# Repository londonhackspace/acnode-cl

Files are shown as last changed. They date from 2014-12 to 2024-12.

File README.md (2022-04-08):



Table of Contents
=================

  * [Table of Contents](#table-of-contents)
  * [Features](#features)
  * [Parts list](#parts-list)
    * [For the transistor switch](#for-the-transistor-switch)
    * [For the rest of the node:](#for-the-rest-of-the-node)
    * [Making the transistor switch](#making-the-transistor-switch)
    * [Wiring in the arcade switch](#wiring-in-the-arcade-switch)
    * [How to get this running with a cooqrobot/elechouse pn532 breakout board:](#how-to-get-this-running-with-a-cooqrobotelechouse-pn532-breakout-board)
    * [Using the tool running pin](#using-the-tool-running-pin)
  * [Building and flashing the firmware](#building-and-flashing-the-firmware)
  * [Pin assignments:](#pin-assignments)
  * [using the CLI](#using-the-cli)
  * [Roles](#roles)
  * [Button status/colours:](#button-statuscolours)
  * [To use the button menu:](#to-use-the-button-menu)
    * [For maintainers the menu items are:](#for-maintainers-the-menu-items-are)
    * [So for a user to take a tool out of service:](#so-for-a-user-to-take-a-tool-out-of-service)
    * [For a maintainer to access the menu and do nothing:](#for-a-maintainer-to-access-the-menu-and-do-nothing)
    * [For a maintainer to add a card:](#for-a-maintainer-to-add-a-card)
  * [Glossary](#glossary)
    * [Offline and Online](#offline-and-online)
    * [In service and Out of service](#in-service-and-out-of-service)

# Features

* Command line interface for settings over the usb port

* Stores settings in eeprom

* Can log to a syslog server

* Uses DHCP to get it's ip address

* Optional pin to detect when a tool is running - good for detecting when consumables are being used

* Can record the total runtime of of the tool if the tool running pin is used.

* Button with RGB led for status.

* Single Button menu for adding cards and putting a tool off and online.

* Can cache 752 cards to the embedded eeprom.

# Parts list

## For the transistor switch

* 1 x NPN transistor, i used a 2N3904
* 1 x 1K resistor
* 1 x small bit (8 x 8 holes is fine) of Vero board
* 2 x C shaped crimp or solderable terminals for the relay
* 2 x wires with female header socket ends (the other end doesn't matter, and will be cut off), one black, and one red.
* 1 x black female to female header socket lead
* 1 x grey female to female header socket lead

## For the rest of the node:

* 2 x crimp or solderable spade terminals for the microswitch on the arcade button
* 2 x wires with female header socket ends (the other end doesn't matter, and will be cut off), one black & one white
* 1 x PN532 based card reader
* 1 x connected Launchpad TM4C1294XL
* 1 x red  female to female header socket lead
* 1 x blue female to female header socket lead
* 1 x green female to female header socket lead
* 1 x black female to female header socket lead

##  Making the transistor switch

* cut one end off the 2 wires with header socket ends, leaving as much wire
as possible and the female ends

* Strip the bare end crimp into the terminals - for the arcade button
terminals use a white and black wire, and for the relay use red and black
wires.

* Attach the red wire to the+ side of the VDC connections on the SSR and the
black one to the - side.

* Attach the red female and to +5v header pin on the launchpad

* On some strip board solder the transistor on one edge with the flat side
facing the rest of the board.

* Cut the track connected to the middle (base) pin of the transistor in the
middle of the board

* Solder the 1K resistor over the hole you've cut

* Solder a 3 pin header so the middle pin goes header -> 1k resistor ->
middle (base) of the transistor, and the left and right pins are connected
to the left and right pin of the transistor

Picture of stripboard + transistor + header:

https://pointless.net/photos/id/1419346624/

Picture of the bottom showing cut track:

https://pointless.net/photos/id/1419346632/

* with the header pins towards you looking edge on at the board (the flat
side of the transistor should be facing you), the pins are, from left to
right:

* 1 connect to GND on the connected launchpad with a black female to female lead.
* 2 connect to PG_1 on the connected launchpad
* 3 connect to - on the ssr VDC side with the black lead you made eairler

## Wiring in the arcade switch

* make two spade terminal leads, one white and one black

like this:

https://pointless.net/photos/id/1419334749/

* connect the black one to the bottom of the microswitch on the button and the other end to a convenient GND on the launchpad

* connect the white end to the terminal labelled "NO" on the microswitch, and the other end to PF_1 on the launchpad

* connect the white lead of the RGB led leads to +5V on the launchpad

* the RGB red, green and blue leads go to PM0, PM1 and PM2

## How to get this running with a cooqrobot/elechouse pn532 breakout board:

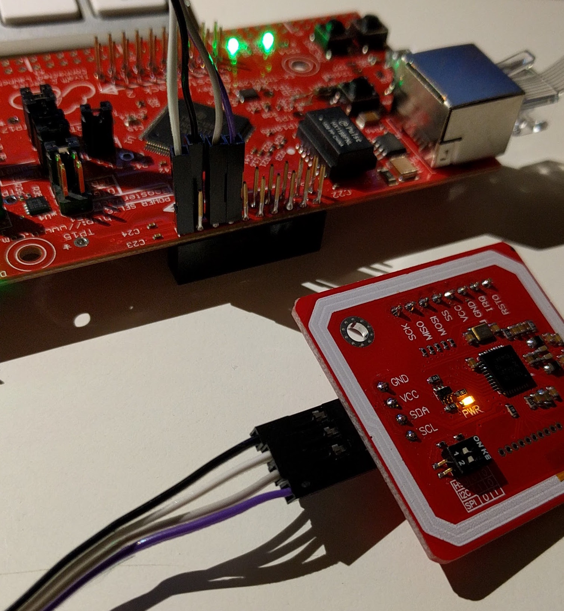
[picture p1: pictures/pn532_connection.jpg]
pn532 connected


1. Cooqrobot boards: Carefully unsolder the 0 ohm resistor jumper from the HIS0 connector, then resolder it (or just bridge the pads with solder) so that the '0' side is connected rather than the 1, this puts the reader in HSU mode.
  Elechouse boards: Set the DIP switches both to the right (This is as shipped from the factory) to put the reader into HSU mode.

2. Solder headers onto the 8 pin connector on the board where the TX/RX pins are, you need at least TX,RX,5V,GND. N.B. Cooqrobot boards: you can't use the SCL/SDA pins on the 4 pin connector because they have pullups on them...

2. Connect 5v and GND to somewhere convenient on the connected launchpad

4. This sketch uses Serial6 which uses PP0 and PP1, AKA pins 43 and 44 on the connected launchpad, connect those too, PP0 goes to TX on the board and PP1 to RX.

5. Check the labels on the card reader boards carefully, one cheap reader board has the pins for the FTDI cable pinouts *backwards* on the top (component) side of the board. Also some card readers label TX and RX the other way round... Do not use cheap Elechouse NFC Reader V3 clones - they often have the wrong component values in their antenna matching stage, and cannot energise cards well. Genuine Elechouse NFC Reader V4 (Direct from Elechouse, work well, the extra price is worth it for avoiding the hassle of deploying an under-performing reader).

See here for the Connected Launchpad pinouts:

http://energia.nu/pin-maps/guide_tm4c129launchpad/

## Using the tool running pin

You can send a signal to the acnode via pin PE_4 to say when your tool is actually running (as opposed to being switched on), useful for keeping track of wear and tear and consumables etc.

# Building and flashing the firmware

(non-PlatformIO version, tested on MacOS 10.12.6, 10.14.4 and Ubuntu 18.04)

* Install git for your platform if you haven't already
* Install cmake for your platform (http://cmake.org , debian/ubuntu package: cmake, MacOS homebrew: `brew install cmake`)
* Create a build directory `mkdir build`
* Run `./gettoolchain.sh`
* Update/initialise the git submodules `git submodule update --init`
* Use cmake to make a Makefile, and define your target board (EK-TM4C1294XL)
  `cd build && cmake .. -DCMAKE_TOOLCHAIN_FILE=../targets/tivac-launchpad/EK-TM4C1294XL.cmake`
  If building on MacOS, you may need to put the cmake binary on your path if you downloaded it manually or refer to it as
  /Applications/CMake.app/Contents/bin/cmake
* Use Gnu make to actually run the dependencies, compile and link: `make -j`
* When ready to upload the resultant elf binary to the Launchpad, `make -j flash`

# Pin assignments:

* PG_1 - active high, switches power to the tool, output
* PF_1 - the button, active low (uses internal pulllup), input
* PM_0 - RGB button Red channel, output
* PM_1 - RGB button Green channel, output
* PM_2 - RGB button Blue channel, output
* PP_0 - Serial RX from the card reader, input (should connect to TX on the card reader)
* PP_1 - Serial TX to the card reader, output (should connect to RX on the card reader)
* PE_4 - tool running pin, active low (uses internal pullup), input
* PD_0 - SD Card MISO (pin 7) aka D0
* PD_1 - SD Card MOSI (pin 2) aka CMD
* PD_3 - SD card clock (pin 5)
* PC_7 - SD card CS (pin 1) aka CD

# Pin assignments on ACNode shield rev 1 board (square PCB)

Other ACnode PCBs are available, the most common at the moment is the hardware/NEW-ACNode-Dootbot-Shield designed by dawidekziaja

* P1 connector (numbers rising towards on-board relay, P1_1 is furthest from it)
* P1_1 GND -> CAT5 ORANGE
* P1_2 +3.3V    NOT CONNECTED
* P1_3 PP0 RX ->  CAT5 WHITE/GREEN -> PN532 TXD
* P1_4 PP1 TX -> CAT5 GREEN -> PN532 RXD

* P3 connector (numbers rising towards reset button)
* P3_1 +3.3V
* P3_2 Red LED -> CAT5 BLUE
* P3_3 Green LED -> CAT5 WHITE/BROWN
* P3_4 Blue LED -> CAT5 BROWN

* P4 connector (numbers rising away from reset button)
* P4_1 +5V -> CAT5 WHITE/ORANGE
* P4_2 
* P4_3 GND

Button connector / Doorbell or ACnode menu button
* PF_1 SWITCH -> CAT5 WHTE/BLUE
* GND 

Door release button
* PM6 SWITCH -> Normally Open
* GND

* Note that Deek-Robot and Elechouse branded PN532 boards need +5V not +3.3v to function. 
Use the pinouts labelled on the back of the board.
Other boards (Genuine Elechouse NFC module v3) sort of work at +3.3V, but may not give sufficient juice to the NFC target to energise certain types of cards.

# Reader installation

For convenience of installation (acnode), and added security (doorbot), we recommend the reader module itself should be connected via an 8 wire cable, such as CAT5, and housed with a pushbutton NO switch and RGB LED in its own enclosure. This way, any intruder can't attack the reader and easily gain access. CAT5 (or above) wiring as above. Note the requirement for 220 ohm resistors on the Red/Green/Blue LED pins to prevent LED burnout. For operational convenience, it is advised to keep a spare reader that can be swapped out. Readers for doorbot enclosures can fit into standard single EN 60670-1 socket boxes with blanking plates, or outdoor junction boxes. For outdoor fitting, ensure that any holes for the button are suitably sealed against moisture ingress. Ditto for ACnode readers in a dusty or dirty environment. 

# Common reader enclosures

## ACnode role
Schneider Electric P/N SL00925 100x100x500 junction box smooth walls has been used for ACnode enclosures in the past. (Farnell DPN10/10 161706)
[ Internal free space 80x80x35mm to brim, there's 10mm outside of this area, compromised by the  mounting posts for the cover ]
[ Cover free space 80x80x16mm to brim, there's 10mm outside of this area, compromised by the mounting posts for the cover ]
Arcade Button with 5V Common Cathode RGB LED, from https://www.arcadeworlduk.com/, e.g. Ultralux RGB Illuminated Arcade Button, mounting hole required 28mm diameter hole in side of enclosure.
Mount PN532 reader and breakout board on the lid
(Optional - use RJ45 modular jack on the side of the enclosure and run a small patch lead to the breakout board, or find a suitable way of terminating the CAT5). Ideally, the readers are easily swappable between ACnodes, so mod jack on the side is a good plan.
Mount modular jack on opposide side of enclosure box to arcade button.

## Internal doorbot role

BS EN 60670-1 45mm deep single socket box with blanking plate
5V Common Cathode RGB LED
N/O SPST push button for doorbell. Choose one that doesn't accidentally get triggered while swiping.
Mount PN532 reader and breakout board on the blanking plate. Wire RJ45 CAT5 cable within walls.
## External doorbot role

British General WPJBS IP55 external junction box from B&Q
[ Internal free space 50x60x35mm, 8mm outide this space, compromised by the mounting posts for the cover ]
5V Common Cathode RGB LED
N/O SPST push button, *water resistant*. Choose one that doesn't accidentally get triggered while swiping.
Run CAT5 cable through a sealed grommit on the rear through the wall.

Pin Assignments
* +5V : RJ45_1 : WHITE/ORANGE : +5V
* GND : RJ45_2 : ORANGE : GND
* PP_0 : RJ45_3 : WHITE/GREEN : -> PN532 TXD
* PM_0 : RJ45_4 : BLUE : VIA R220 - RGB RED 
* PF_1 : RJ45_5 : WHITE/BLUE : the button, active low (uses internal pulllup), input
* PP_1 : RJ45_6 : GREEN : PN532 RXD
* PM_1 : RJ45_7 : WHITE/BROWN : VIA R220 - RGB Green
* PM_2 : RJ45_8 : BROWN : VIA R220 - RGB BLUE

# Power supply

For ACnodes, then a Power over Ethernet micro-USB power splitter works a treat. Feed the 5V USB power straight to the OTG micro USB connector near the ethernet jack, and jumper the Power Select to OTG. Make sure you connect to a network port that is supplied via a PoE network switch.
For doorbots, you will need +12V to power the door solenoid, and ideally, a battery backup. Feed the +12V into the London Hackspace doorbot board so that it goes via a regulator to supply +5V to the Launchpad via the BoosterPack connector. Jumper the launchpad's Power Select to OTG.

# using the CLI

Once the firmware has been uploaded to the connected launchpad connect with a serial terminal (if you use a real one rather than the Energia serial monitor you get command history and line editing).
It will work a lot better if it's connected to a working ethernet port with DHCP at this point.

Use `help` to see a brief description of commands. You want to set the nodeid and toolname as the minimum:

```
nodeid <id>
name <name of tool>
server <acserver hostname>
port <http port to use>
secret <shared secret, see acserver tool config>
syslog <syslog server to use>
mqtt_topic_base <mqtt_topic_base e.g. /tool/selfclearingdesk >
maintainercache - toggle maintainer cache mode (stores maintainers credentials in EEPROM so it should still work for maintainers after complete power loss)
```

and then `save` to save the settings.

It is good practice to make a note of the MAC address of the acnode, and reserve a DHCP reservation on the router for it, because then it can be monitored by icinga or other monitoring system.

# Button status/colours:

* Starting up: rainbow cycling
* In service, idle: blue
* In service, valid user, tool on: green
* In service, invalid user: red
* In service, maintainer: yellow
* Out of service, idle: flashing blue/red
* Out of service, valid user: red (and the tool will be off)
* Out of service, maintainer: yellow (and the tool will turn on)
* Doorbell pressed: Long Orange / Blue / Orange / Blue
* Door released: Green
* Door access denied: Red

# Roles

Each node can work in a variety of roles:

## Regular ACNode (0)

Provided that a card known to the system is presented, and it has access to this particular tool, the relay is active
as long as the card is on the reader.

## Doorbot (1)

Provided that a card known to the system is presented, the relay is activated for `KEEP_OPEN_MILISECONDS` (1.5 seconds).

## Doorbot with access control (2)

Provided that a card known to the system is presented, and it has access to this particular tool (door), the relay
is activated for `KEEP_OPEN_MILISECONDS` (1.5 seconds).

## Audit only (3)

Provided that a card known to the system is presented, the relay is active as long as the card is on the reader.
This is used primarily for logging what user was using a tool at what time.

# To use the button menu:

A short press starts the menu and switches between items, a long press selects a menu item.

For users the only menu item is to take the tool out of service - it's flashing red/green

The menu also times out after 60 seconds.

## For maintainers the menu items are:

* Add a user (flashing Amber)
* Take the tool out of service (if it's in service) - flashing red
* put a tool in service (if it's out of service), flashing green.

## So for a user to take a tool out of service:

Press the button once, quickly, the button will be flashing red/green.

Hold the button down for a second or so and release.

The button will go solid red and the tool will be out of service

## For a maintainer to access the menu and do nothing:

press the button once, the button will flash Amber/yellow - the ACNode is in add mode.

press the button again, the button will flash red/yellow - the menu is in take tool out of service mode.

press the button again, the button will stop flashing, you have exited the menu.

## For a maintainer to add a card:

Press the button, it will flash Amber/yellow

press the button for 1 second or so and let it go, the button will go yellow

remove the maintainer card. add the card to be added - the button will go orange (invalid card colour)

remove the card.

The new card should now be added.

# Glossary

## Offline and Online

The tool does not (or does) have a working network connection to the acserver. Things that can make an ACNode offline include:

* network cable unplugged
* Ethernet switch powered off or dead
* DHCP server down
* dns server down
* acserver VM down
* acserver VM running, but no acserver running
* acserver running, but crashing or having problems (e.g. database down, no cards in database)

## Nice to have services

The list of dependencies that are nice to have, but not strictly necessary

* mqtt server should be up, if announce_mode is set to mqtt (now default on new installs)

## In service and Out of service

Manually set by a maintainer or user - users can set a tool out of service, only a maintainer can put a tool in service, in/out of service state is kept in the acserver database and on the ACNode it's self
In doorbot or doorbot access control roles, in-service or out of service has no meaning, and has no way of setting this state, other than via the acserver itself.

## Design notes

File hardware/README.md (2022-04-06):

# How to make an ACnode or Doorbot

Over the years the design of the ACnodes and doorbots have been gradually improved.

As of 2021-10-28, all acnodes and doorbots in London Hackspace have been using the 'New-ACNode-Doorbot-Shield' designs. This is a single PCB designed to
fit **underneath** a TI Tiva C XL Connected Launchpad microcrontroller board EK-TM4C1294XL EVAL BRD, TIVA C CONNECTED LAUNCHPAD. The Launchpad boards are normally available from Farnell and RS.

There are plans for an all-new doorbot/acnode board together with a reader module, but they are not as yet ready for use. This is to address interference on long cable runs between the acnode/doorbot board and reader.

The board features an on-board 5V coil relay that is suitable for switching up to 10A of 230V. If you need to switch anything greater, then use it to
energise the coil of an appropriate contactor.

Build up the ACnode board as per kicad schematics. On rev 1.1b, component values are silkscreened for easy assembly. You will require long header pins so that the Launchpad board sits above the relay. Hint when soldering the long header pins into this board - use a Launchpad upside-down as a jig to hold the pins, place the pins, place the ACnode board upside-down, then solder them. Once soldered, a blob of hot glue is advised to keep the long header pins spaced and prevent bending them when handling in future.
When building the board for the ACnode role, you may omit the LM7805 voltage regulator if you're only going to be providing it with +5V power.

Always ensure that any metal enclosure is suitably earthed.

## Doorbot role

You will require

- A +12V power supply, approximately 3A at 12V should be enough to energise a maglock or solenoid lock. You can't use POE for this, it won't provide enough current for a maglock.
- Optional: A sealed lead acid battery, recommended for exterior doors. The doorbot software is designed to handle power outages with no networking available.
- A suitable helpfully labelled DOOR EXIT button, SPDT or DPDT, must be able to handle the current of whatever lock you choose. We will use two poles to both interrupt the current to the lock (NC contact) and to signal the doorbot to hold the door open for a time.
- Some CAT5 or higher wiring and connectors to run a cable to the reader module.
- Some suitable wire. We've found that old +12V DC power cables for CCTV cameras is suitable for the 12V lock circuit.
- A suitable enclosure
- A micro-USB to laptop cable, of suitable length, for configuration and flashing the software.
- A maglock with bracket, or solenoid deadbolt. 12V DC.

## ACnode role

You will require

- A +5V power supply, most decent USB power supplies work well, and you can get POE splitters that will provide this via Micro USB as well. Most of the London Hackspace network switches support POE. This is normally the recommended solution.
- Some CAT5 or higher wiring and connectors to run a cable to the reader module.
- Knowledge of the tool that you are providing access control to. Ideally, you'd be switching a low(er) voltage control circuit like an e-stop, rather than turning full power on and off to the tool. For high current switching, use an external suitably sized mains contactor.
- optional: a tool-running input, like on the laser cutter, the AC node can log the time the tool was running.
- suitable enclosure, or suitable space within the tool for the board. DIN rail mounting is recommended, 3D printed DIN-rail clips have been known to work with the board glued to the clips. Where we need a standalone enclosure, we have used TA 241911 ENCLOSURE BOX, GREY, IP65, 240X191X107MM, Farnell Part number 1422671
- A micro-USB to laptop cable, of suitable length, for configuration and flashing the software.

Set the power select jumper on the Launchpad board to 'OTG', and plug your USB power supply into the 'OTG' interface, we'll use that to provide power to the microcontroller.

## Reader enclosure

Typically used for ACnode roles.
Can use any suitable enclosure, but ideally one deep enough for the arcade button, and a RJ45 modular connector. https://uk.farnell.com/schneider-electric/dpn10-10/box-abs-103x103x56mm/dp/161706 has worked well.
For a laser-cut card holder front-end, see the dxf files in this repository's hardware/ directory. These will need M2.5 nylon nuts to hold the stack of laser cut acrylic together through to the front cover of the reader.
We have typically used arcade microswitch buttons with LED. " Ultralux RGB Illuminated Arcade Button " from Arcade World UK. https://www.arcadeworlduk.com/products/ultralux-rgb-illuminated-arcade-button.html

For doorbot roles, we typically build the readers into standard socket boxes with blanking plates. Exterior card readers will need a suitably watertight enclosure with a watertight button.
Drilling a standard EN 60670-1 thermosetting plastic blanking plate to fit LED and buttons makes them prone to cracking. Start with a tiny pilot drill, ideally in a drill press, and work up sizes. Fortunately, they are cheap and very easy to come by (wilko,screwfix,B&Q).
RJ45 termination to a modular jack is typically within the enclosure rather than external as on most of the acnode role readers.
PN532 RFID reader module: Set to HSS mode. Elechouse V4. Order direct from Elechouse. Do not skimp on ordering from aliexpress or ebay, because there are huge numbers of clones with AWFUL antenna matching circuitry.

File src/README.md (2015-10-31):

Table of Contents
=================

  * [Table of Contents](#table-of-contents)
  * [Features](#features)
  * [Parts list](#parts-list)
    * [For the transistor switch](#for-the-transistor-switch)
    * [For the rest of the node:](#for-the-rest-of-the-node)
    * [Making the transistor switch](#making-the-transistor-switch)
    * [Wiring in the arcade switch](#wiring-in-the-arcade-switch)
    * [How to get this running with a cooqrobot/elechouse pn532 breakout board:](#how-to-get-this-running-with-a-cooqrobotelechouse-pn532-breakout-board)
    * [Using the tool running pin](#using-the-tool-running-pin)
  * [You will need these libraries:](#you-will-need-these-libraries)
    * [Syslog from here:](#syslog-from-here)
    * [the PN532 libraries from here:](#the-pn532-libraries-from-here)
    * [DateTimeLibrary](#datetimelibrary)
    * [SD Card Library](#sd-card-library)
  * [Pin assignments:](#pin-assignments)
  * [using the CLI](#using-the-cli)
  * [Button status/colours:](#button-statuscolours)
  * [To use the button menu:](#to-use-the-button-menu)
    * [For maintainers the menu items are:](#for-maintainers-the-menu-items-are)
    * [So for a user to take a tool out of service:](#so-for-a-user-to-take-a-tool-out-of-service)
    * [For a maintainer to access the menu and do nothing:](#for-a-maintainer-to-access-the-menu-and-do-nothing)
    * [For a maintainer to add a card:](#for-a-maintainer-to-add-a-card)
  * [Glossary](#glossary)
    * [Offline and Online](#offline-and-online)
    * [In service and Out of service](#in-service-and-out-of-service)

# Features

* Command line interface for settings over the usb port

* Stores settings in eeprom

* Can log to a syslog server

* Uses DHCP to get it's ip address

* Optional pin to detect when a tool is running - good for detecting when consumables are being used

* Can record the total runtime of of the tool if the tool running pin is used.

* Button with RGB led for status.

* Single Button menu for adding cards and putting a tool off and online.

* Can cache 752 cards to the embedded eeprom.

# Parts list

## For the transistor switch

* 1 x NPN transistor, i used a 2N3904
* 1 x 1K resistor
* 1 x small bit (8 x 8 holes is fine) of Vero board
* 2 x C shaped crimp or solderable terminals for the relay
* 2 x wires with female header socket ends (the other end doesn't matter, and will be cut off), one black, and one red.
* 1 x black female to female header socket lead
* 1 x grey female to female header socket lead

## For the rest of the node:

* 2 x crimp or solderable spade terminals for the microswitch on the arcade button
* 2 x wires with female header socket ends (the other end doesn't matter, and will be cut off), one black & one white
* 1 x PN532 based card reader
* 1 x connected Launchpad
* 1 x red  female to female header socket lead
* 1 x blue female to female header socket lead
* 1 x green female to female header socket lead
* 1 x black female to female header socket lead

##  Making the transistor switch

* cut one end off the 2 wires with header socket ends, leaving as much wire
as possible and the female ends

* Strip the bare end crimp into the terminals - for the arcade button
terminals use a white and black wire, and for the relay use red and black
wires.

* Attach the red wire to the+ side of the VDC connections on the SSR and the
black one to the - side.

* Attach the red female and to +5v header pin on the launchpad

* On some strip board solder the transistor on one edge with the flat side
facing the rest of the board.

* Cut the track connected to the middle (base) pin of the transistor in the
middle of the board

* Solder the 1K resistor over the hole you've cut

* Solder a 3 pin header so the middle pin goes header -> 1k resistor ->
middle (base) of the transistor, and the left and right pins are connected
to the left and right pin of the transistor

Picture of stripboard + transistor + header:

https://pointless.net/photos/id/1419346624/

Picture of the bottom showing cut track:

https://pointless.net/photos/id/1419346632/

* with the header pins towards you looking edge on at the board (the flat
side of the transistor should be facing you), the pins are, from left to
right:

* 1 connect to GND on the connected launchpad with a black female to female lead.
* 2 connect to PG_1 on the connected launchpad
* 3 connect to - on the ssr VDC side with the black lead you made eairler

## Wiring in the arcade switch

* make two spade terminal leads, one white and one black

like this:

https://pointless.net/photos/id/1419334749/

* connect the black one to the bottom of the microswitch on the button and the other end to a convenient GND on the launchpad

* connect the white end to the terminal labelled "NO" on the microswitch, and the other end to PF_1 on the launchpad

* connect the white lead of the RGB led leads to +5V on the launchpad

* the RGB red, green and blue leads go to PM0, PM1 and PM2

## How to get this running with a cooqrobot/elechouse pn532 breakout board:

1. carefully unsolder the 0 ohm resistor jumper from the HIS0 connector, then resolder it (or just bridge the pads with solder) so that the '0' side is connected rather than the 1, this puts the reader in HSU mode.

2. Solder headers onto the 8 pin connector on the board where the tx/rx pins are, you need at least tx,rx,3.3v,gnd. N.B. you can't use the SCL/SDA pins on the 4 pin connector because they have pullups on them...

2. Connect 3.3v and gnd to somewhere convenient on the connected launchpad

4. This sketch uses Serial6 which uses PP0 and PP1, AKA pins 43 and 44 on the connected launchpad, connect those too, PP0 goes to TX on the board and PP1 to RX.

5. Check the labels on the card reader boards carefully, one cheap reader board has the pins for the FTDI cable pinouts *backwards* on the top (component) side of the board. Also some card readers label TX and RX the other way round...

See here for the Connected Launchpad pinouts:

http://energia.nu/pin-maps/guide_tm4c129launchpad/

## Using the tool running pin

You can send a signal to the acnode via pin PE_4 to say when your tool is actually running (as opposed to being switched on), useful for keeping track of wear and tear and consumables etc.

# You will need these libraries:

## Syslog from here:

https://github.com/londonhackspace/Syslog

put it in the libraries folder under your energia sketches folder

## the PN532 libraries from here:

https://github.com/londonhackspace/PN532

You'll need to copy or symlink PN532 and PN532_HSU into your energia-sketches libraries directory as well.

## DateTimeLibrary

https://github.com/londonhackspace/DateTimeLibrary

Best to clone directly to your Energia libraries folder.

If you a are using Energia 16 you will need to patch the energia code with this change:

https://github.com/energia/Energia/pull/741/files

## SD Card Library

https://github.com/rei-vilo/SD_TM4C

(and rename it to 'SD'), [also see](http://jasiek.me/2015/08/28/using-an-sd-card-with-a-ti-tiva-c-tm4129.html) for some more details.

# Pin assignments:

* PG_1 - active high, switches power to the tool, output
* PF_1 - the button, active low (uses internal pulllup), input
* PM_0 - RGB button Red channel, output
* PM_1 - RGB button Green channel, output
* PM_2 - RGB button Blue channel, output
* PP_0 - Serial RX from the card reader, input (should connect to TX on the card reader)
* PP_1 - Serial TX to the card reader, output (should connect to RX on the card reader)
* PE_4 - tool running pin, active low (uses internal pullup), input
* PD_0 - SD Card MISO (pin 7) aka D0
* PD_1 - SD Card MOSI (pin 2) aka CMD
* PD_3 - SD card clock (pin 5)
* PC_7 - SD card CS (pin 1) aka CD

# using the CLI

Once the firmware has been uploaded to the connected launchpad connect with a serial terminal (if you use a real one rather than the Energia serial monitor you get command history and line editing).

Use `help` to see a brief description of commands. You want to set the nodeid and toolname as the minimum:

```
nodeid <id>
name <name>
server <acserver hostname>
port <http port to use>
syslog <syslog server to use>
```

and then `save` to save the settings.

# Button status/colours:

* Starting up: yellow
* In service, idle: blue
* In service, valid user, tool on: green
* In service, invalid user: orange
* In service, maintainer: yellow
* Out of service, idle: flashing blue/red
* Out of service, valid user: red (and the tool will be off)
* Out of service, maintainer: yellow (and the tool will turn on)

# To use the button menu:

A short press starts the menu and switches between items, a long press selects a menu item.

For users the only menu item is to take the tool out of service - it's flashing red/green

The menu also times out after 60 seconds.

## For maintainers the menu items are:

* Add a user (flashing Amber)
* Take the tool out of service (if it's in service) - flashing red
* put a tool in service (if it's out of service), flashing green.

## So for a user to take a tool out of service:

Press the button once, quickly, the button will be flashing red/green.

Hold the button down for a second or so and release.

The button will go solid red and the tool will be out of service

## For a maintainer to access the menu and do nothing:

press the button once, the button will flash Amber/yellow - the ACNode is in add mode.

press the button again, the button will flash red/yellow - the menu is in take tool out of service mode.

press the button again, the button will stop flashing, you have exited the menu.

## For a maintainer to add a card:

Press the button, it will flash Amber/yellow

press the button for 1 second or so and let it go, the button will go yellow

remove the maintainer card. add the card to be added - the button will go orange (invalid card colour)

remove the card.

The new card should now be added.

# Glossary

## Offline and Online

The tool does not (or does) have a working network connection to the acserver. Things that can make an ACNode offline include:

* network cable unplugged
* Ethernet switch powered off or dead
* DHCP server down
* dns server down
* acserver VM down
* acserver VM running, but no acserver running
* acserver running, but crashing or having problems (e.g. database down, no cards in database)

## In service and Out of service

Manually set by a maintainer or user - users can set a tool out of service, only a maintainer can put a tool in service, in/out of service state is kept in the acserver database and on the ACNode it's self

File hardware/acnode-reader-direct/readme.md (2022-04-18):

# AC node / doorbot breakout board
rev 1.1a

Designed in kicad 6

designed to connect an RJ45 socket to an Elechouse V4 NFC module
without spaghetti wiring.

Inspired by Liam's solder-pad version.

Initial revision of this is targeted at EN 60670-1 socket back-boxes / blanking plate builds as used by Doorbots.
There's no reason not to use them for acnodes as well, but a near-future revision (possibly before ordering the boards)
will include support for the existing boxes used for AC node builds with the massive arcade buttons, by means of different
mounting holes.

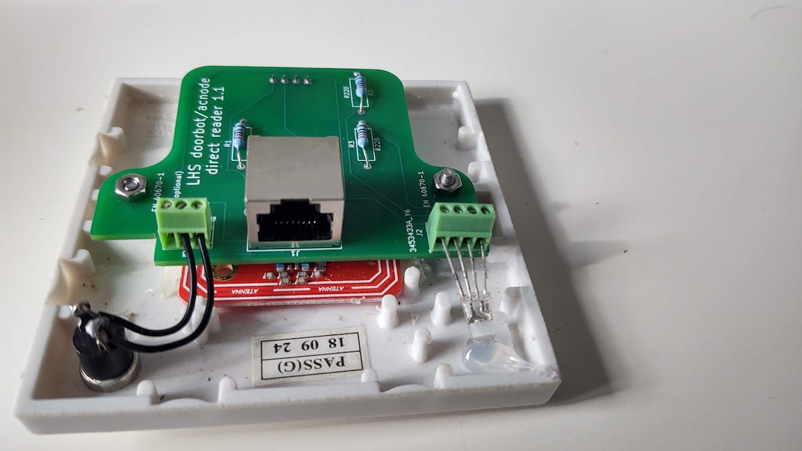
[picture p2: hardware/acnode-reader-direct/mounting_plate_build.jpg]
Blanking Plate build


# Errata

rev 1.1: J2 RGB LED silkscreen is labelled backwards. Should read B- G- +5 R-, with R- closest to the middle of the board, corrected in rev 1.1a

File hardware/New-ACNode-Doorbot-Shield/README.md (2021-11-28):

# acnode-doorbot
A board designed to be used for ACNode and Doorbot at London Hackspace
# Board View and 3D Render
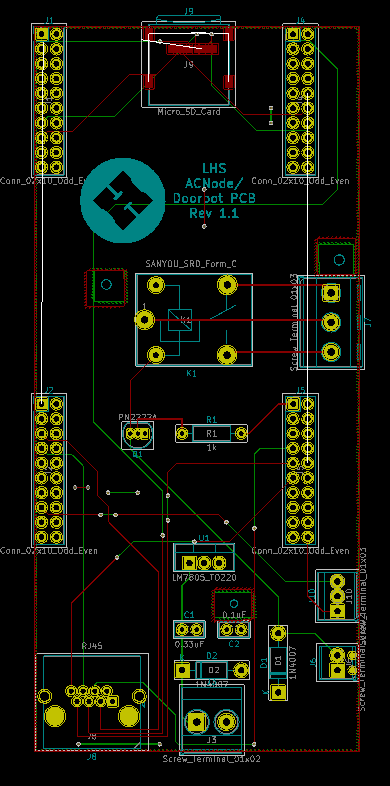
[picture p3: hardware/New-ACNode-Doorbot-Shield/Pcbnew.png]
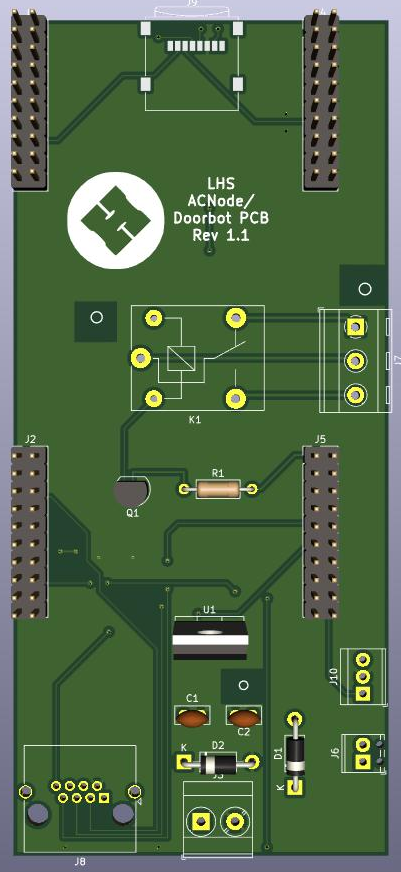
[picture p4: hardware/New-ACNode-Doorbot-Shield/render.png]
 

# Errata
rev 1.1 : RJ45 connector is round the wrong way
rev 1.1a : Relay outputs silkscreen is labelled incorrectly. NC is actually on the side closest to the SD card connector, not the voltage regulator side which is NO.

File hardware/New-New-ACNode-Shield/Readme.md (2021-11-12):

This is yet another board. IT IS NOT YET READY FOR USE!

It's basically a backport of the design I came up with for a Nucleo-based version. Key features include:
* An LED on the board for debugging
* A button on the board for debugging
* Support for RS-422 reader connection
* SPI Flash instead of SD Card
* Opto-isolated tool on input
* Trasistor-buffered door release with ferrite beads

Things to fix before the next version:

* Launchpad ethernet connector fouls the shield
* LED is... rather bright...
* A jumper on the ISL3176 ~RE line would allow a single board to support 5V and 12V readers
* Footprints for 3.81mm connectors are too tight - holes too small

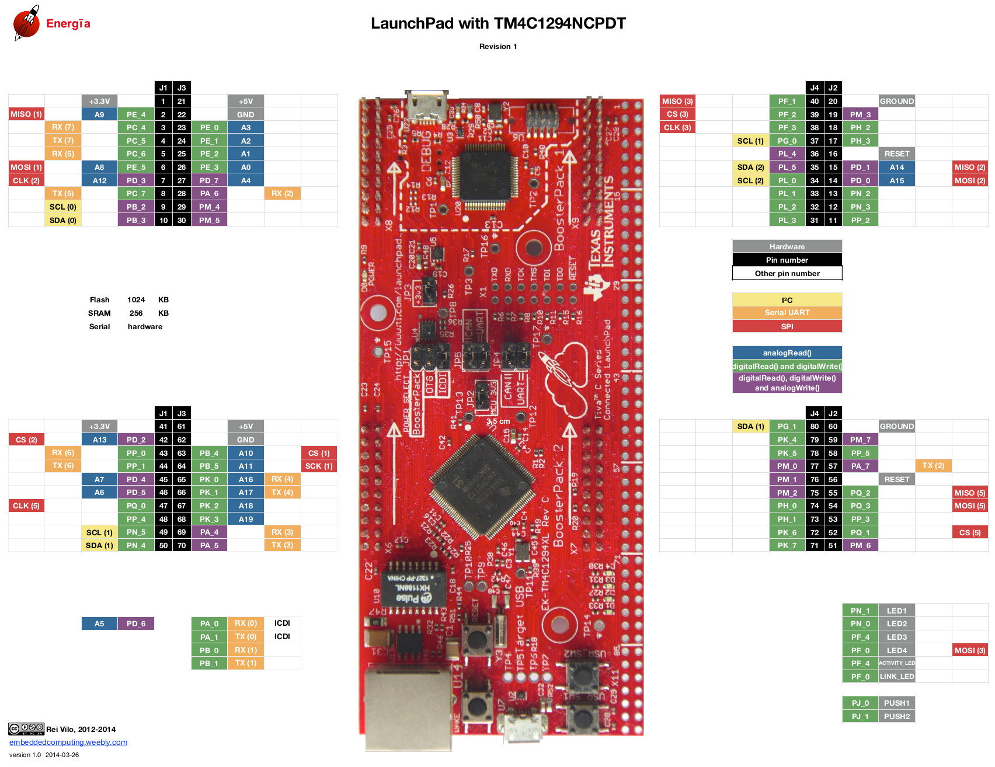
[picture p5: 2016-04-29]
pictures/EK-TM4C1294XL.jpg

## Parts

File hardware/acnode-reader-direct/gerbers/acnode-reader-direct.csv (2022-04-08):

Id | Designator | Package | Quantity | Designation | Supplier and ref
1 | J3 | TerminalBlock_TE_282834-3_1x03_P2.54mm_Horizontal | 1 | BUTTON N/O
2 | J1 | RJ45_Amphenol_RJHSE5380 | 1 | RJ45
3 | EN 60670-1,EN 60670-1 | MountingHole_3.7mm | 2 | MountingHole_3.7mm
4 | R1,R2,R3 | R_Axial_DIN0309_L9.0mm_D3.2mm_P12.70mm_Horizontal | 3 | R220
5 | J2 | TerminalBlock_TE_282834-4_1x04_P2.54mm_Horizontal | 1 | R- +5 G- B-
6 | LED HOLE | MountingHole_5.3mm_M5 | 1 | MountingHole_5.3mm_M5
7 | J4 | PinSocket_1x04_P2.54mm_Horizontal | 1 | Conn_01x04

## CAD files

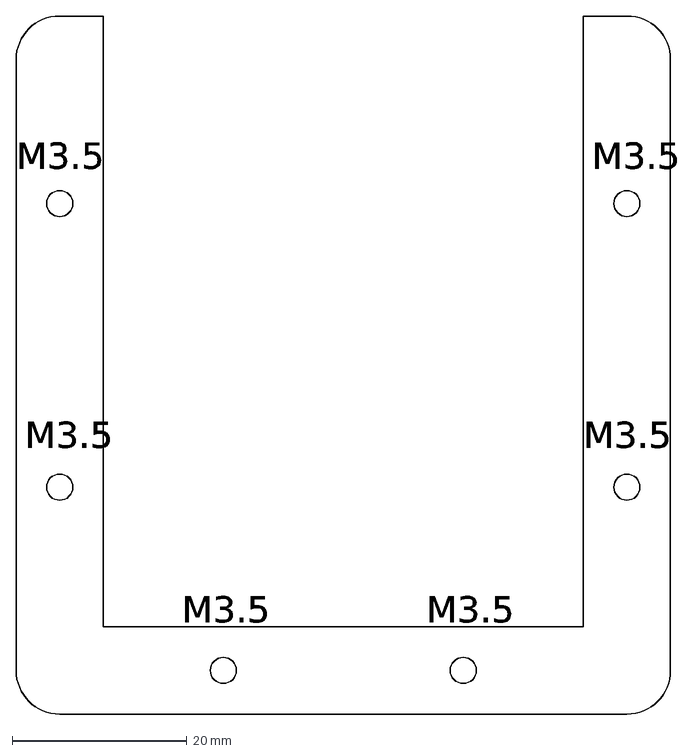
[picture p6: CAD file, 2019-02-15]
hardware/Card front middle.dxf
M3.5

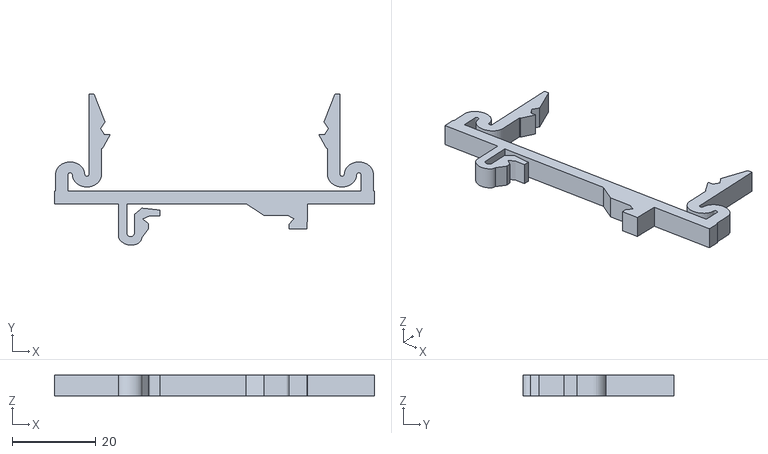
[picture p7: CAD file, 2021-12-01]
hardware/New-ACNode-Doorbot-Shield/dinrail_clip.stl
76.5 x 36.2 x 5.00

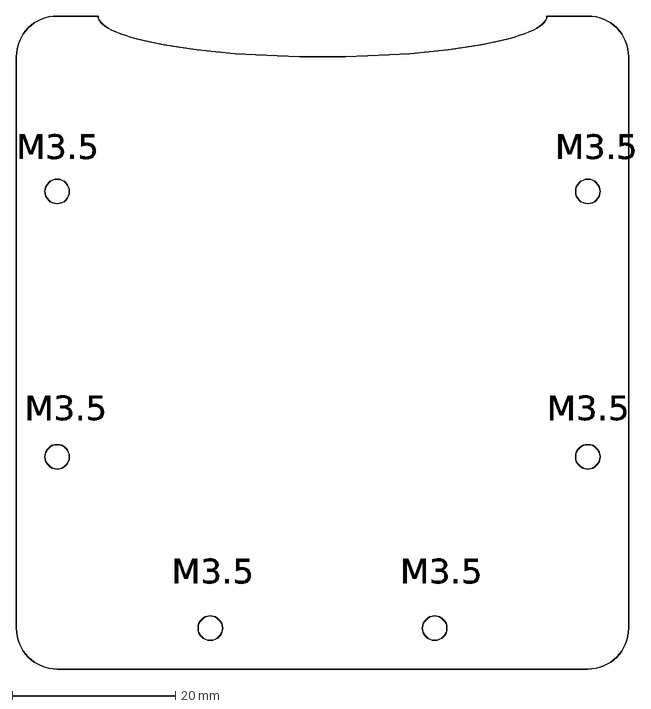
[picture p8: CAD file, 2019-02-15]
hardware/Card front.dxf
M3.5

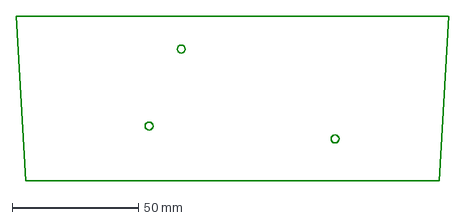
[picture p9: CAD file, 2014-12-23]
hardware/backing-frame.dxf
171.2 x 65.0 mm

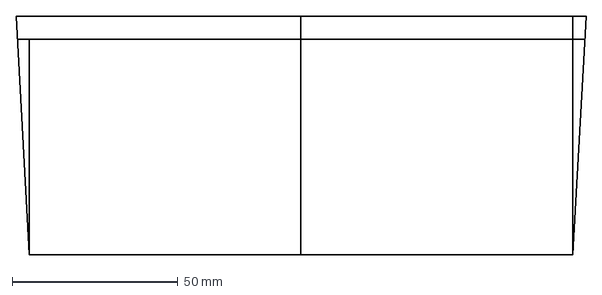
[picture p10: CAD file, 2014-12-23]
hardware/backing-v1.dxf
172.0 x 72.0 mm

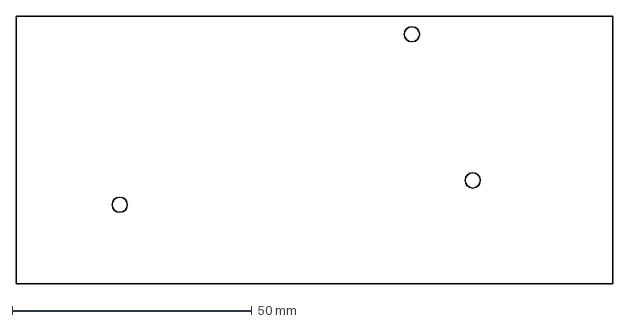
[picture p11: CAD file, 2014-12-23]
hardware/launchpad-footprint.dxf
124.5 x 55.9 mm

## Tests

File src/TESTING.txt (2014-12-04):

Check that:

A valid user switches the tool on
A vaild maintainer switches the tool on
A card that exists in the system but does not have perms does not switch the
tool on
A card that does not exist in the system does not switch the tool on

Check that card status changes correctly update the cache:

no perm -> perm
no perm -> maintainer
perm -> no perm
perm -> maintainer
maintainer -> no perm
maintainer -> perm

a maintainer can add a card
a maintainer can take an in service tool out of service (and is cached)
a maintainer can take an out of service tool in service (and is cached)
a normal user can take an in service tool out of service (and is cached)

check that cached users work when the acnode is disconnected
check that tool in service/out of service works when the acnode is disconnected

XXX what happend to tool status if we:

Are disconnected, a maintainer puts the tool out of service, the acnode is
reconnected and rebooted - it will query the server, the server will tell
the acnode that it should be in service and the acnode will put it back into service,
is that what we want?

Is the acnode or the acserver the authoritive source of the in/out of service status?

button colours:

tool starting up: yellow
tool in service, with net connection: blue
tool in service, no net connection: flashing orange/blue
tool out of service: red

Tool in service, and running: green
Tool in service, and running with a maintainer: yellow
Tool in service, card with no permissions: orange
tool in service, card not recognised: orange (would have to add more state
to recognise this case)

bugs:

clear does not work? (or maybe we need to re-read the settings?).
spams syslog if tool offline.
  - we need a "new user detected function"
the user stuff should be a class
new/delete, pointers and references, malloc and free is all a bit crazy.

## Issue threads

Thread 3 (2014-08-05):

work out what extra hardware we need and add them.

JasperWallace, 2014-08-05:
- RGB led?
- Reset button?
- Other button(s)? (e.g. "tool has failed button)
- methods of switching mains power on and off, we have an SSR, would be nice to have a range of options for different current draws
- last but not least, a decent enclosure

zymurgic, 2020-03-21:
Fairly stable set of acnodes has been deployed at Wembley. This ticket is old and can be closed.

Closed 2020-03-21.

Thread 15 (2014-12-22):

no pn532 reader with new connected launchpad

JasperWallace, 2014-12-22:
With a new connected launchpad the pn532 reader dosn't get initialised and the code hangs.

If you comment out all the stuff that calls the card reader, get to the cli, set a nodeid and save the settings the board can then talk to the card reader.

I have no idea why this happens :frowning: :confounded: :confused:

UKTamo, 2015-02-19:
Seems like new boards are Rev D that don't like working...

UKTamo, 2015-02-19:
Doesn't appear to be bringing the Tx line unto 3v3

Closed 2015-09-11.

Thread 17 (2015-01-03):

Add watchdog timer in case of crashes

russss, 2015-01-03:

JasperWallace, 2015-01-14:
http://forum.stellarisiti.com/topic/587-watchdog/
https://github.com/yuvadm/tiva-c/blob/master/boards/ek-lm4f232/watchdog/watchdog.c
https://github.com/energia/Energia/blob/master/hardware/lm4f/cores/lm4f/driverlib/watchdog.h
https://github.com/energia/Energia/blob/master/hardware/lm4f/cores/lm4f/driverlib/watchdog.c

Closed 2015-09-11.

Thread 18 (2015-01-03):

Laser cutter acnode crashes

russss, 2015-01-03:
We're seeing occasional crashes on the laser cutter acnode. This manifests itself either as the light staying blue when a card is presented, or the light staying yellow/green when the card is removed.

russss, 2015-01-03:
Adding watchdog (#17) may be enough to deal with this, at least initially.

JasperWallace, 2015-01-05:
if the watchdog times out it will powercycle the tool when the acnode restarts, better then nothing tho :disappointed: :crying_cat_face:

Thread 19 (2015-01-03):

Laser cutter acnode loses card

russss, 2015-01-03:
The laser cutter acnode is sometimes losing the card and switching the tool off.

This could be an issue with the card going out of range, as the reader is now stuck to the top of the box and there's no card slot.

However it should be noted that this has happened a few times when the card has definitely not moved at all. Additionally, it seems like moving the card around does not cause the acnode to re-acquire the card until the card has been completely removed and replaced. So there might be something else going on here.

zymurgic, 2019-03-19:
laser cutter acnode needs a bit of a rebuild to better match the other acnodes, with the reader in a slot.

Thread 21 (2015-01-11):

Check that we cope with running out of space to cache users, we already have 60 on the laser cutter!

JasperWallace, 2015-01-11:

JasperWallace, 2015-09-08:
We currently have 629 cards for the laser cutter.

An acnode using the eeprom for storage has space for 752 cards.

Closed 2015-09-08.

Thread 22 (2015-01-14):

minimum power on time

JasperWallace, 2015-01-14:
Some cards seem to glitch a little and only switch the acnode on for a fraction of a second. It's probably not good for the laser cutter when that happens!

So check how long we have been running on tool.off() and if < 1 second wait a few seconds before switching off.

Closed 2015-09-12.

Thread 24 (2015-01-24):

syslog logging is less verbose

JasperWallace, 2015-01-24:
It used to log:

local0.notice<133>: Jan 11 15:12:26 LaserCutter Tool On for 042B51BA5A1E80
local0.notice<133>: Jan 11 15:25:47 LaserCutter Tool off after running for 00:13:20 for 042B51BA5A1E80
local0.notice<133>: Jan 11 15:25:47 LaserCutter Total run time now: 00:13:20

but now just logs:

local0.notice<133>: Jan 12 14:34:22 LaserCutter Tool switched on for 04701E52E72280

The 'off'  and 'total run time' lines have got lost for some reason :disappointed:

UKTamo, 2015-01-24:
That's because tool time is done via the optothingy on the lasercutter

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

russss, 2015-01-24:
Yeah, we moved the time logging back to coolbot to try and debug the
crashing. We can probably put it back now that we know the new code wasn't
at fault.
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

JasperWallace, 2015-09-08:
ok, so not a bug

Closed 2015-09-08.

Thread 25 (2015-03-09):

Add a heartbeat

marksteward, 2015-03-09:
So we can see when the client dies, and catch failed "Access Finished" requests, so should probably include the "in-use" flag.

JasperWallace, 2015-03-10:
calling a uri on the acserver?

I can add a heartbeat eaisly with an Every().

marksteward, 2015-03-10:
Yeah! Like /ping or /heartbeat or summat. Happy to add the server-side

UKTamo, 2015-03-10:
Can we tie this into the ACNode checking acserver for status, and if the DB
says out of service, and the node says in service, the DB wins?

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

marksteward, 2015-03-10:
Yeah, maybe we should just call networkCheckToolStatus every minute. If the server doesn't see 3 requests in a row, it assumes the tool's no longer in use?

JasperWallace, 2015-05-10:
ead6d54bed62234c205fb647f28d224b559f47ab (and 972cccbbdfe9c13b47bd7feb1c9dbf3db78bf578) ended up calling networkCheckToolStatus every 2 seconds.

I can make that longer if needed, but part of that change was that we wanted a way to shut down a tool remotely, potentially in a hurry...

UKTamo, 2015-05-10:
Why an I getting these

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

JasperWallace, 2015-05-10:
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

You opened the bug originally, so github assumes you want to read the replies, I'm not sure if it possible to reassign a bug to someone else...

--

Jonty, 2015-05-10:
You can unsubscribe from the thread by hitting the "unwatch" button on the right.

UKTamo, 2015-05-10:
Ta

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

Closed 2015-05-10.

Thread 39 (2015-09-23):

watchdog will timeout if no network cable attached

JasperWallace, 2015-09-23:
I think dhcp had a 60 second timeout.

JasperWallace, 2015-09-27:
actually it doesn't, not sure what happened then...

Closed 2015-09-27.

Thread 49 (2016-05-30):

Replace the colour coded RGB button with something colour blind friendly

mentarus, 2016-05-30:
The single RGB button was a great idea for a simple interface but it makes it impossible to distinguish the state of the machine for some colour-blind maintainers. I don't think there's an "easy" solution for this, maybe adding a simple LCD screen should be considered?

russss, 2016-05-30:
A cheap LCD is going to be equally inaccessible to those with bad eyesight. Do we have someone who's red-blue colour-blind?

mentarus, 2016-05-30:
red-green actually

russss, 2016-05-30:
OK, I think we could sort it out with a software tweak. I'll give it a think.

JasperWallace, 2016-05-31:
I'm happy to run some tests with different colours to find ones that can be distinguished

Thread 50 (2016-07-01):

MicroSD slot on the PCB is the wrong size, needs adjusting.

jasiek, 2016-07-01:
Pads for the MicroSD holder are not correctly aligned with the actual part - needs redoing.

zymurgic, 2019-03-25:
We've got a new PCB design anyway, and the micro SD hinges fit this one fine.

Closed 2019-03-25.

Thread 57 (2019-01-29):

acnodes need to fail gracefully in event of network failure to acserver

zymurgic, 2019-01-29:
In the event of network failure between a booted acnode and acserver, it shouldn't mis-interpret the failure to connect to acserver as a tool-should-be-out-of-service error.
especiallly when the tool is currently in use.
it should also be able to gracefully fall back to using cached credentials, especially where it's using sdcard or eeprom card caches.

Today, this occurred when a network switch crashed and failed to forward packets), taking out both the 3d printers.

zymurgic, 2019-07-09:
acserver has been moved to the same VLAN as the acnodes themselves, which removes one point of failure. Still reliant on working network switches, but no longer reliant (at least from a packet-forwarding perspective) on a working router/firewall. Still requires DHCP leases to be able to renew or fail gracefully; A working DNS resolver is still very useful.

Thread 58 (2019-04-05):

Lasercutter node seems to be VERY chatty on syslog

mich181189, 2019-04-05:
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

I wonder if these log messages are related the weird run times we're seeing?

zymurgic, 2019-07-08:
If it pages down, or seeing frequent restart messages,  worth noting the acnode is currently powered via the attached Windows PC, which some people shut down. Maybe worth using PoE or similar instead?

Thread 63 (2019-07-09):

When DNS fails, mqtt (and other things) can cause reboots

mich181189, 2019-07-09:
When DNS is down, the resulting connection failures can cause the watchdog timer to be triggered. This is bad because it means the cache is lost

mich181189, 2019-07-13:
When dns fails once things are running, the node will work for a while before potentially getting stuck in a reboot loop.

What’s nasty is this can happen even if there is a cached card, because of the rebalidation.

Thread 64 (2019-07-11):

Unexplained hang of 1st floor dootbot

zymurgic, 2019-07-11:
Power was good to launchpad. 4.65V at VBUS should be good enough.
No response to card reader, or doorbell
No response to serial console.
No repsonse to ICMP.
Reset button fixed it.

mich181189, 2019-07-11:
4.65 sounds a little marginal to me. The microcontroller can, no doubt, handle it fine considering it's a 3.3v part, but I wonder how the board overall deals with it?

mich181189, 2019-07-12:
Launchpad is specified for 4.75-5.25v (source: http://www.ti.com/lit/ug/spmu365c/spmu365c.pdf section 1.6)

zymurgic, 2019-07-12:
will replace the regulator next time I'm in if nobody gets there sooner.

mich181189, 2020-03-20:
Power supply was out of spec - closing this one since it’s otherwise too vague to work on

Closed 2020-03-20.

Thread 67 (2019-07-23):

(hardware) Use of TIG welder near a doorbot reader cable run can fake a doorbell input

zymurgic, 2019-07-23:
Use of a TIG welder (other spark gap transmitters are available) in the vicinity of a doorbot reader cable can induce sufficient negative current in the input to trigger a doorbell notification.
Doorbell / button input is PF_1 on the Launchpad / White/Blue on the CAT5 / pin5, and is normally open, pulled to ground when pushed.

This may affect all microcontroller inputs, and may also be the cause of reported acnode crashes.

Investigate methods of input protection to attempt to prevent this.

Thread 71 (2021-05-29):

Maglock power sense

padski, 2021-05-29:
This is possibly included in a future HW update by Mich, adding here for the record.
Maglock power sense / tool on / door solenoid ..........
It would be great to know when our doors unlock themselves for whatever reason ;)

zymurgic, 2021-08-12:
The solenoid deadbolt locks have a 'door closed' output, which signals when it's properly closed. Those aren't currently wired in, but could go to a 'tool running' input, probably via some optocoupler. Then it's down to the acnode role as doorbot to detect and announce accordingly, which would be alarming or of interest in certain circumstances. However, where the exit button isn't also wired into the door release input but instead only interrupts the +12V power to the solenoid, the acnode wouldn't be aware of the reason for the door opening.

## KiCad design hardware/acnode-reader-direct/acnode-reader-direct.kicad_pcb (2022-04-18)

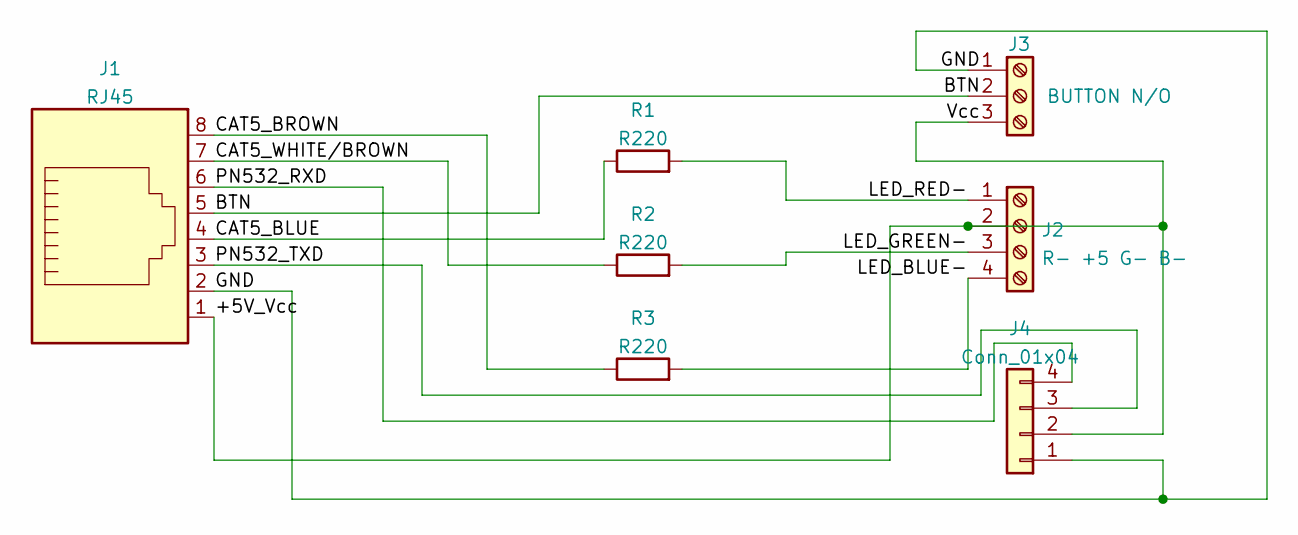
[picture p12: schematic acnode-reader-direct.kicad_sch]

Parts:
J1: RJ45; RJ45_Amphenol_RJHSE5380
J2: R- +5 G- B-; TerminalBlock_TE_282834-4_1x04_P2.54mm_Horizontal
J3: BUTTON N/O; TerminalBlock_TE_282834-2_1x02_P2.54mm_Horizontal
J4: Conn_01x04; PinSocket_1x04_P2.54mm_Horizontal
R1, R2, R3: R220; R_Axial_DIN0309_L9.0mm_D3.2mm_P12.70mm_Horizontal

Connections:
/+5V_Vcc: J1.1, J2.2, J3.3, J4.2
/BTN: J1.5, J3.2
/CAT5_BLUE: J1.4, R1.1
/CAT5_BROWN: J1.8, R3.1
/CAT5_WHITE/BROWN: J1.7, R2.1
/GND: J1.2, J3.1, J4.1
/LED_BLUE-: J2.4, R3.2
/LED_GREEN-: J2.3, R2.2
/LED_RED-: J2.1, R1.2
/PN532_RXD: J1.6, J4.4
/PN532_TXD: J1.3, J4.3

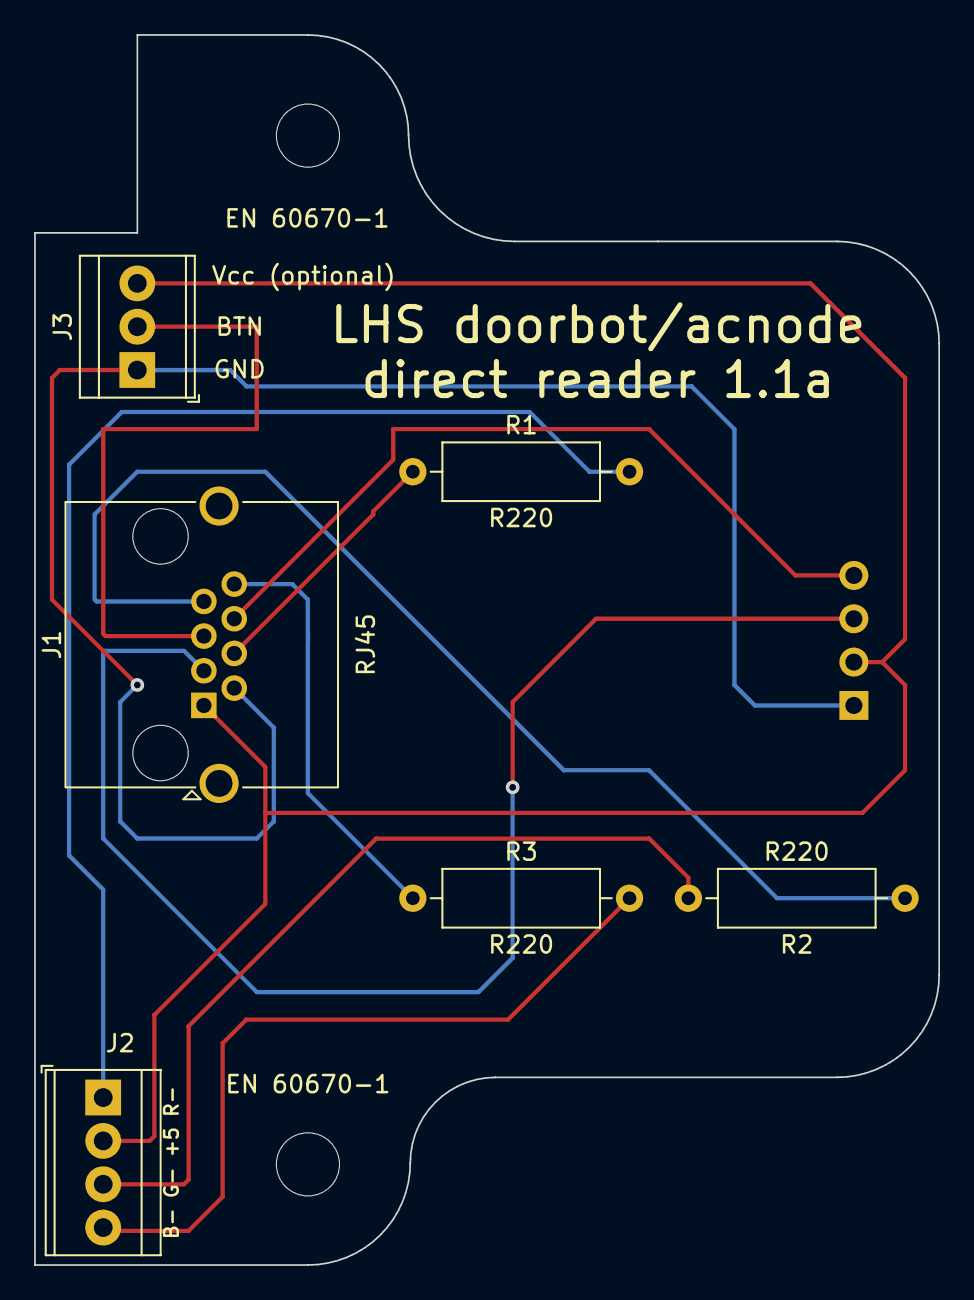
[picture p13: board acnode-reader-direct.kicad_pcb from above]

Board: 2 copper layers, 53.0 x 72.1 mm, 9 parts (1 on the bottom side), 11 nets.

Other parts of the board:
EN 60670-1, EN 60670-1#2: MountingHole_3.7mm

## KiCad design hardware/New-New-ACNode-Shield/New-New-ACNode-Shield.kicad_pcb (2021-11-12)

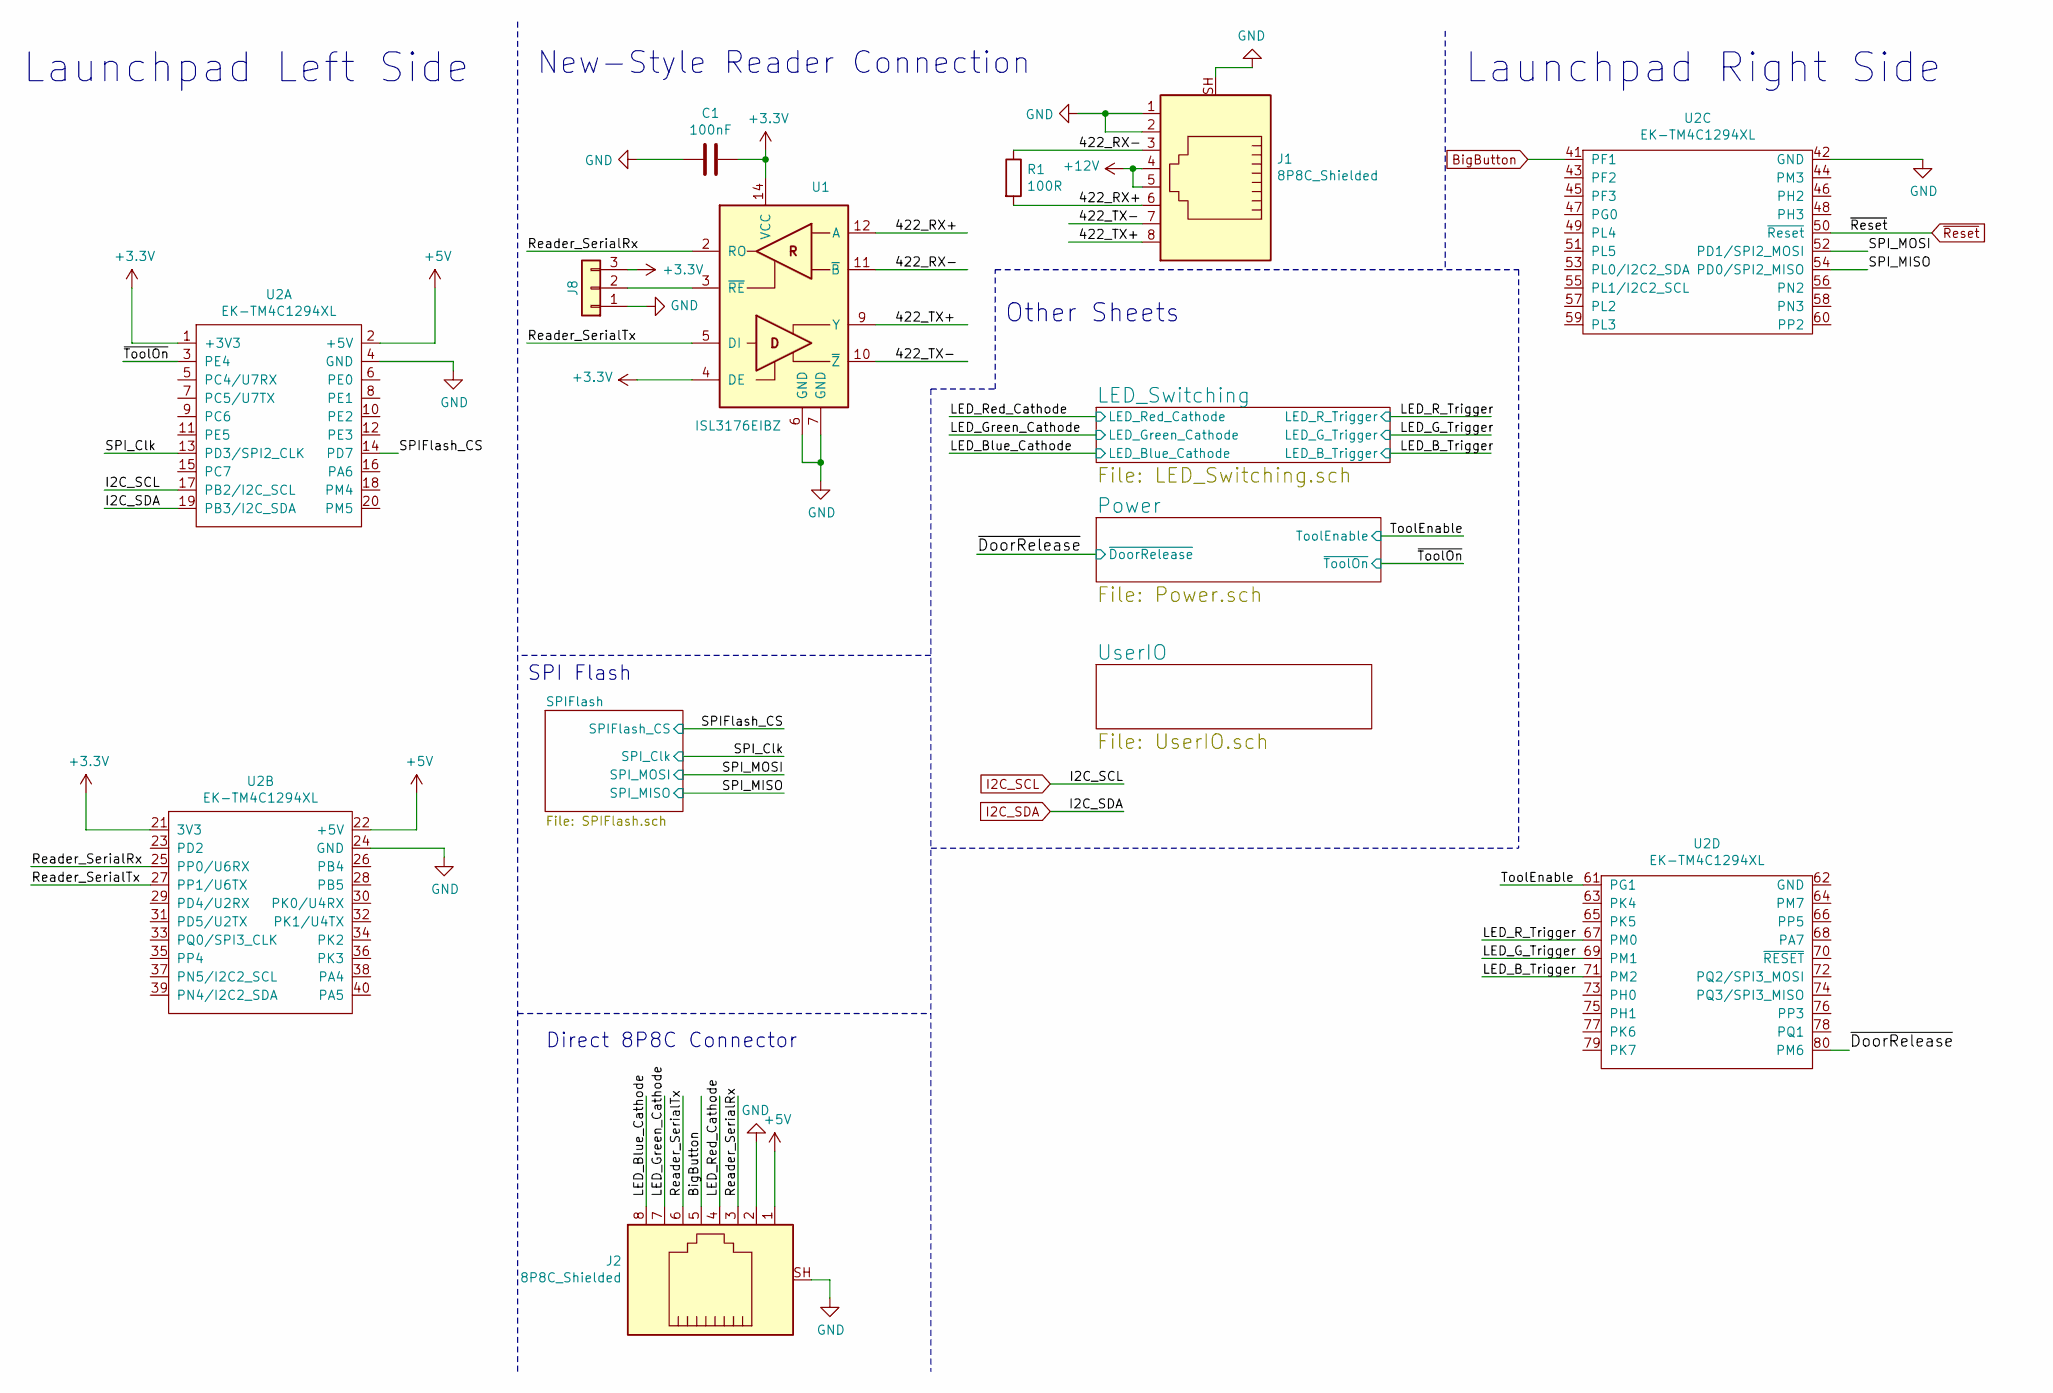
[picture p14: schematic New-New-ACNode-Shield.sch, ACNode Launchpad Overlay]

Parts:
C1: 100nF; C_0603_1608Metric
J1, J2: 8P8C_Shielded; RJ45_Ninigi_GE
J8: Conn_01x03; PinHeader_1x03_P2.54mm_Vertical
R1: 100R; R_0603_1608Metric
U1: ISL3176EIBZ; SOIC-14_3.9x8.7mm_P1.27mm
U2: EK-TM4C1294XL; Launchpad

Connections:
+3V3: C1.1, J8.3, U1.4 (DE), U1.14 (VCC), U2.1 (+3V3), U2.21 (3V3); also elsewhere on the board
+5V: J2.1, U2.2 (+5V), U2.22 (+5V); also elsewhere on the board
+12V: J1.4, J1.5; also elsewhere on the board
/422_RX+: J1.6, R1.2, U1.12 (A)
/422_RX-: J1.3, R1.1, U1.11 (~B)
/422_TX+: J1.8, U1.9 (Y)
/422_TX-: J1.7, U1.10 (~Z~)
/LED_B_Trigger: U2.71 (PM2); also elsewhere on the board
/LED_Blue_Cathode: J2.8; also elsewhere on the board
/LED_G_Trigger: U2.69 (PM1); also elsewhere on the board
/LED_Green_Cathode: J2.7; also elsewhere on the board
/LED_R_Trigger: U2.67 (PM0); also elsewhere on the board
/LED_Red_Cathode: J2.4; also elsewhere on the board
/Reader_SerialRx: J2.3, U1.2 (RO), U2.25 (PP0/U6RX)
/Reader_SerialTx: J2.6, U1.5 (DI), U2.27 (PP1/U6TX)
/SPIFlash_CS: U2.14 (PD7); also elsewhere on the board
/SPI_Clk: U2.13 (PD3/SPI2_CLK); also elsewhere on the board
/SPI_MISO: U2.54 (PD0/SPI2_MISO); also elsewhere on the board
/SPI_MOSI: U2.52 (PD1/SPI2_MOSI); also elsewhere on the board
/ToolEnable: U2.61 (PG1); also elsewhere on the board
/~DoorRelease: U2.80 (PM6); also elsewhere on the board
/~ToolOn: U2.3 (PE4); also elsewhere on the board
BigButton: J2.5, U2.41 (PF1); also elsewhere on the board
GND: C1.2, J1.1, J1.2, J1.SH, J2.2, J2.SH, J8.1, U1.6 (GND), U1.7 (GND), U2.4 (GND), U2.24 (GND), U2.42 (GND); also elsewhere on the board
I2C_SCL: U2.17 (PB2/I2C_SCL); also elsewhere on the board
I2C_SDA: U2.19 (PB3/I2C_SDA); also elsewhere on the board
unnamed: J8.2, U1.3 (~RE)
~Reset: U2.50 (~Reset); also elsewhere on the board

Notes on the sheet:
Launchpad Left Side
Launchpad Right Side
Direct 8P8C Connector
SPI Flash
New-Style Reader Connection
Other Sheets

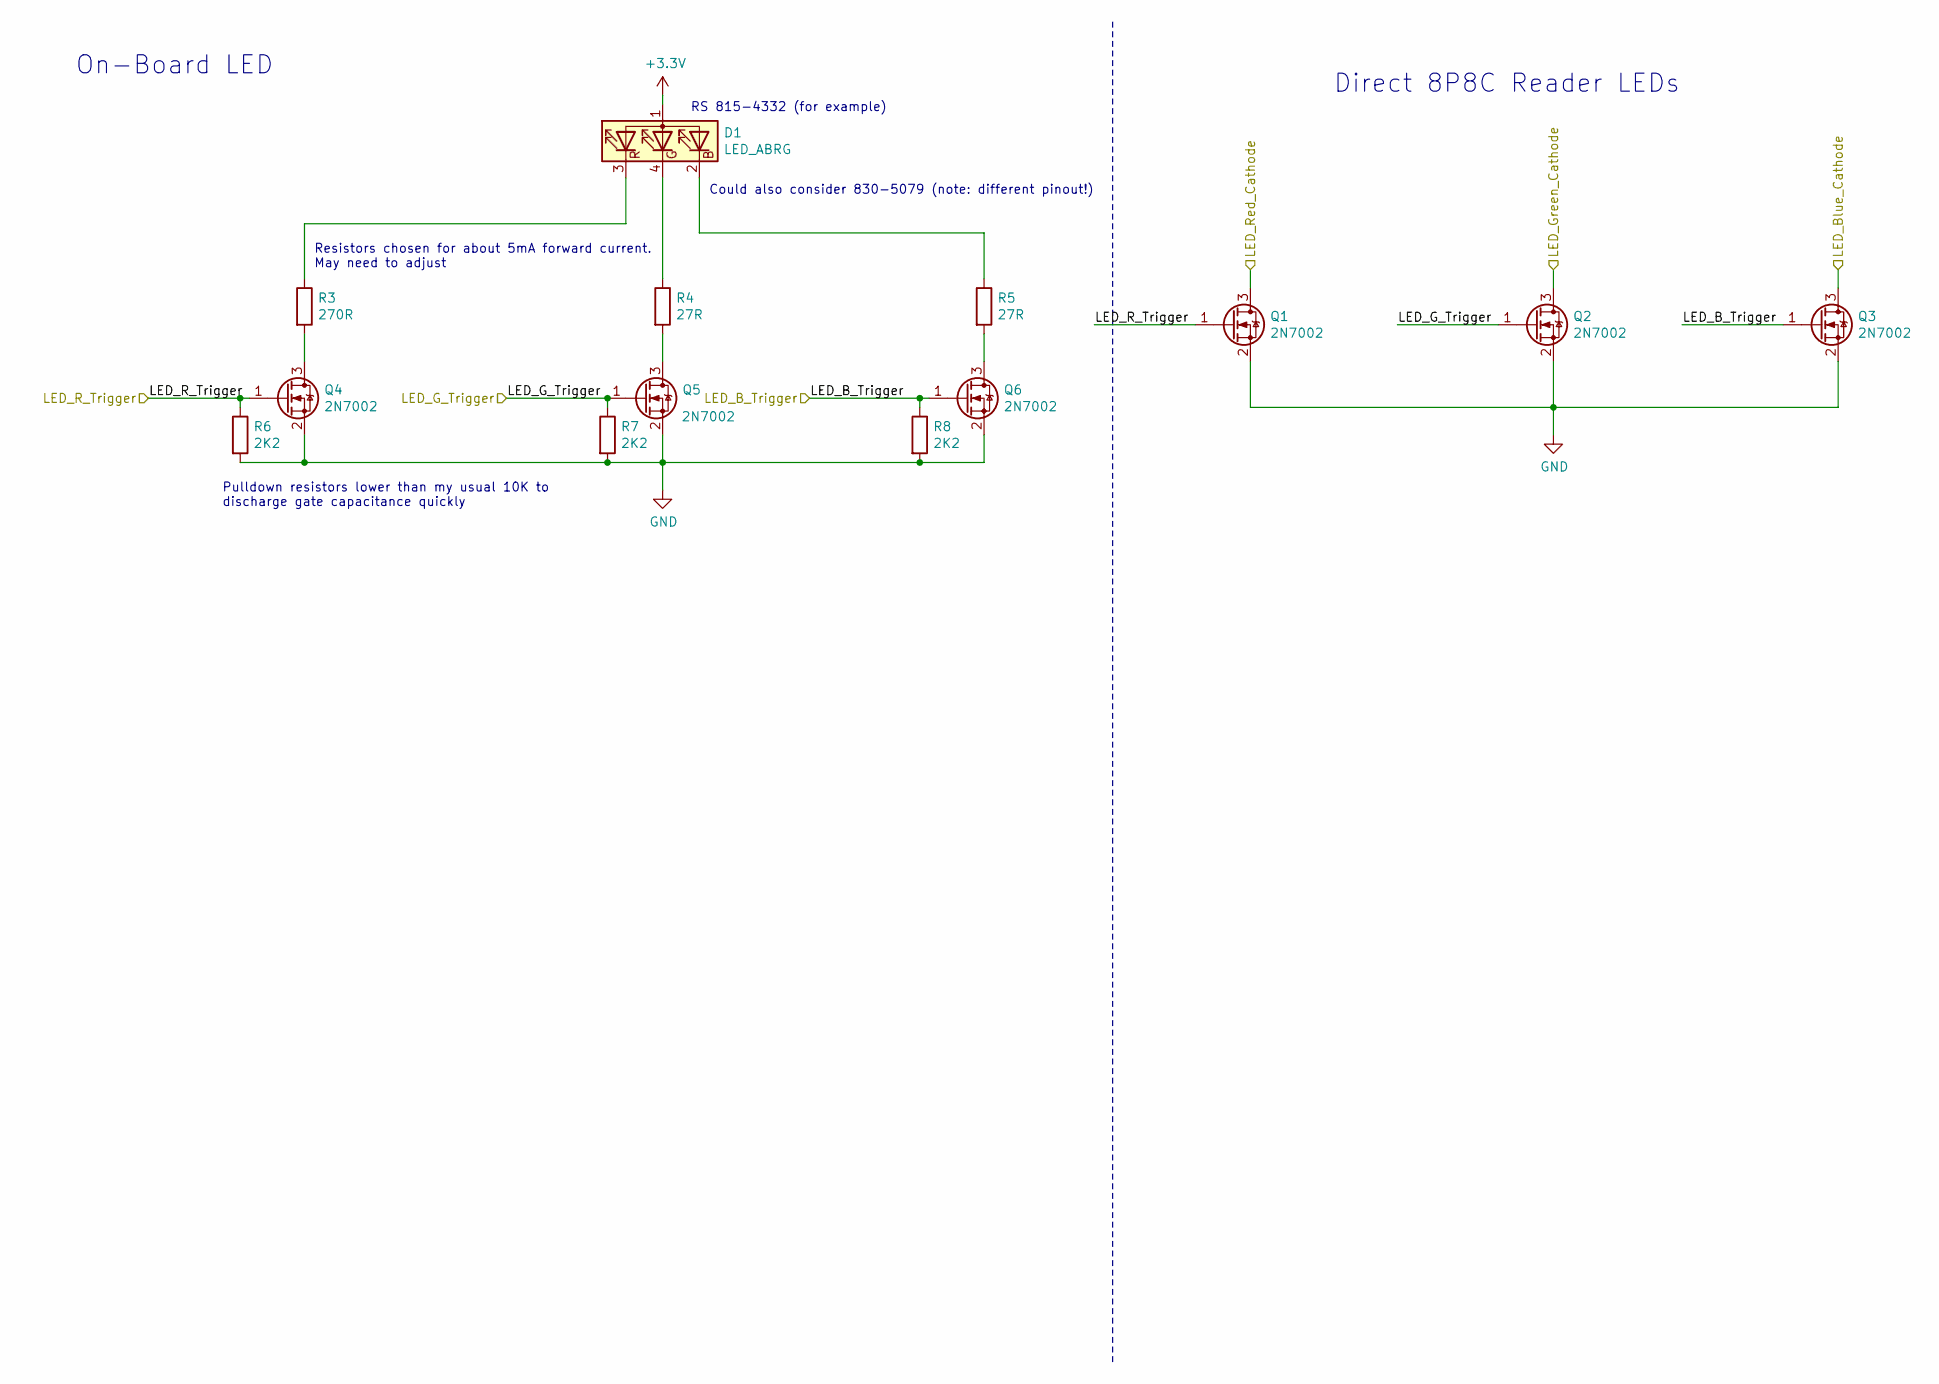
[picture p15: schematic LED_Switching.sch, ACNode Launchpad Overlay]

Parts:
D1: LED_ABRG; Wurth_3528_LED
Q1, Q2, Q3, Q4, Q5, Q6: 2N7002; SOT-23
R3: 270R; R_0603_1608Metric
R4, R5: 27R; R_0603_1608Metric
R6, R7, R8: 2K2; R_0603_1608Metric

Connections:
+3V3: D1.1 (A); also elsewhere on the board
/LED_B_Trigger: Q3.1 (G), Q6.1 (G), R8.1; also elsewhere on the board
/LED_Blue_Cathode: Q3.3 (D); also elsewhere on the board
/LED_G_Trigger: Q2.1 (G), Q5.1 (G), R7.1; also elsewhere on the board
/LED_Green_Cathode: Q2.3 (D); also elsewhere on the board
/LED_R_Trigger: Q1.1 (G), Q4.1 (G), R6.1; also elsewhere on the board
/LED_Red_Cathode: Q1.3 (D); also elsewhere on the board
GND: Q1.2 (S), Q2.2 (S), Q3.2 (S), Q4.2 (S), Q5.2 (S), Q6.2 (S), R6.2, R7.2, R8.2; also elsewhere on the board
unnamed: D1.2 (BK), R5.1
unnamed: D1.3 (RK), R3.1
unnamed: D1.4 (GK), R4.1
unnamed: Q4.3 (D), R3.2
unnamed: Q5.3 (D), R4.2
unnamed: Q6.3 (D), R5.2

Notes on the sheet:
RS 815-4332 (for example)
On-Board LED
Direct 8P8C Reader LEDs
Pulldown resistors lower than my usual 10K to discharge gate capacitance quickly
Could also consider 830-5079 (note: different pinout!)
Resistors chosen for about 5mA forward current. May need to adjust

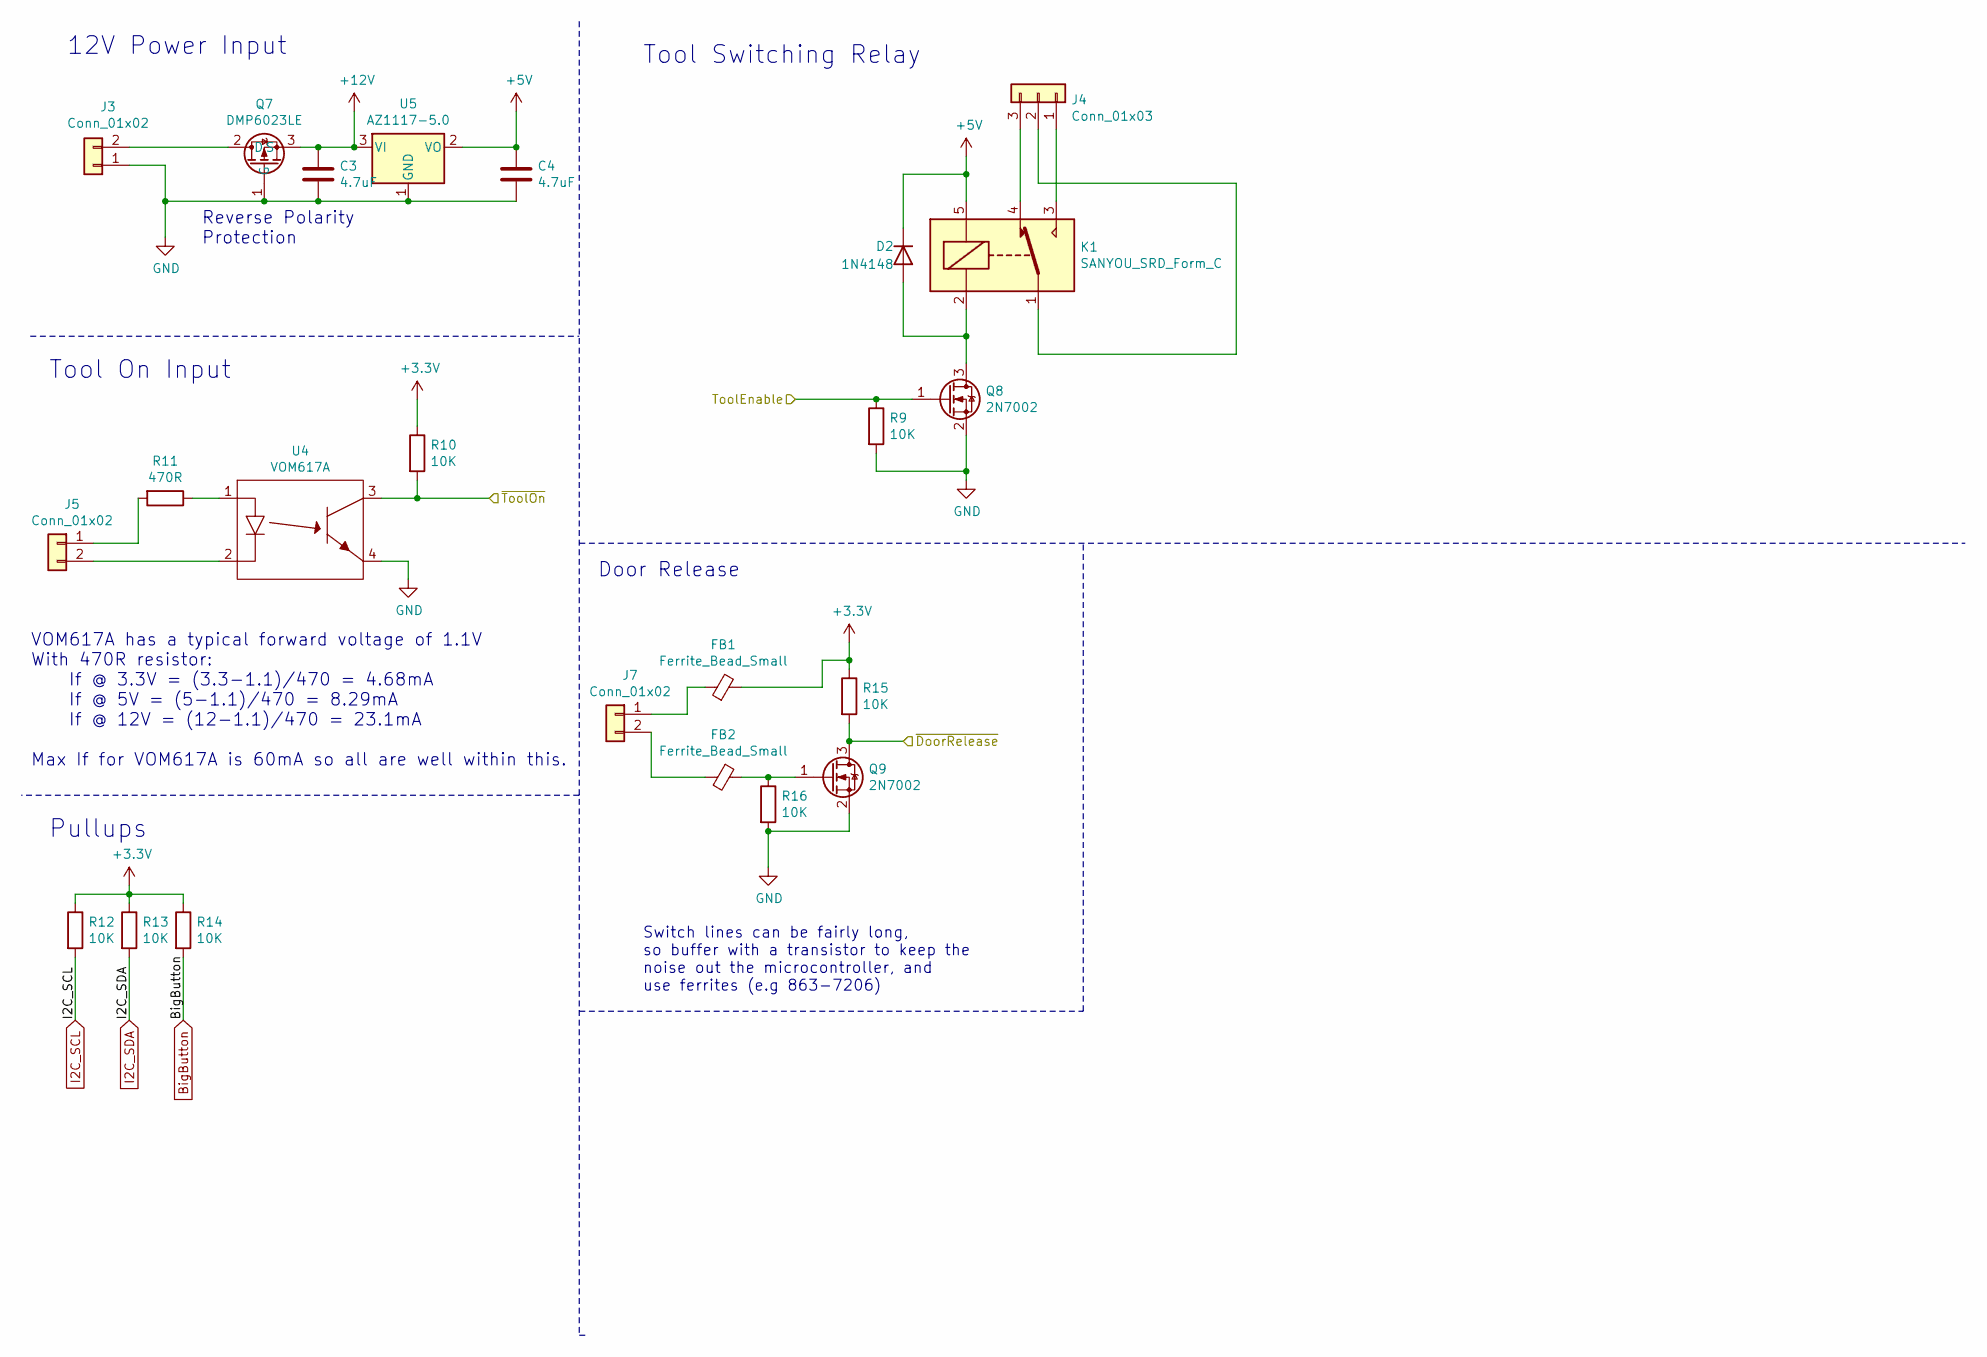
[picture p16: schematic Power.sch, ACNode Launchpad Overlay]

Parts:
C3, C4: 4.7uF; C_0805_2012Metric
D2: 1N4148; D_DO-35_SOD27_P7.62mm_Horizontal
FB1, FB2: Ferrite_Bead_Small; C_0805_2012Metric
J3: Conn_01x02; Connector-5.08mm
J4: Conn_01x03; Connector-3.81mm-3pin
J5, J7: Conn_01x02; Connector-3.81mm-2pin
K1: SANYOU_SRD_Form_C; Relay_SPDT_SANYOU_SRD_Series_Form_C
Q7: DMP6023LE; SOT-223
Q8, Q9: 2N7002; SOT-23
R9, R10, R12, R13, R14, R15, R16: 10K; R_0603_1608Metric
R11: 470R; R_0603_1608Metric
U4: VOM617A; VOM617A-4SOP
U5: AZ1117-5.0; SOT-223-3_TabPin2

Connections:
+3V3: FB1.2, R10.1, R12.1, R13.1, R14.1, R15.1; also elsewhere on the board
+5V: C4.1, D2.1 (K), K1.5, U5.2 (VO); also elsewhere on the board
+12V: C3.1, Q7.3 (S), U5.3 (VI); also elsewhere on the board
/ToolEnable: Q8.1 (G), R9.1; also elsewhere on the board
/~DoorRelease: Q9.3 (D), R15.2; also elsewhere on the board
/~ToolOn: R10.2, U4.3; also elsewhere on the board
BigButton: R14.2; also elsewhere on the board
GND: C3.2, C4.2, J3.1, Q7.1 (G), Q8.2 (S), Q9.2 (S), R9.2, R16.2, U4.4, U5.1 (GND); also elsewhere on the board
I2C_SCL: R12.2; also elsewhere on the board
I2C_SDA: R13.2; also elsewhere on the board
unnamed: D2.2 (A), K1.2, Q8.3 (D)
unnamed: FB1.1, J7.1
unnamed: FB2.1, Q9.1 (G), R16.1
unnamed: FB2.2, J7.2
unnamed: J3.2, Q7.2 (D), Q7.4 (Tab)
unnamed: J4.1, K1.3
unnamed: J4.2, K1.1
unnamed: J4.3, K1.4
unnamed: J5.1, R11.2
unnamed: J5.2, U4.2
unnamed: R11.1, U4.1

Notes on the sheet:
Reverse Polarity Protection
12V Power Input
Tool Switching Relay
Tool On Input
VOM617A has a typical forward voltage of 1.1V With 470R resistor: If @ 3.3V = (3.3-1.1)/470 = 4.68mA If @ 5V = (5-1.1)/470 = 8.29mA If @ 12V = (12-1.1)/470 = 23.1mA Max If for VOM617A is 60mA so all are well within this.
Pullups
Door Release
Switch lines can be fairly long, so buffer with a transistor to keep the noise out the microcontroller, and use ferrites (e.g 863-7206)

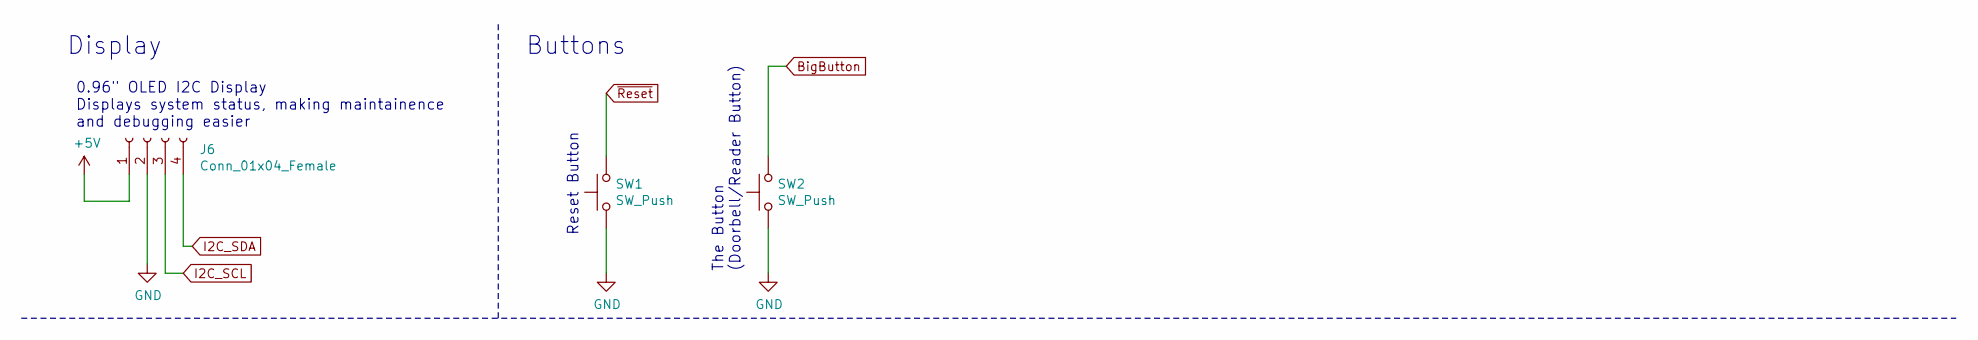
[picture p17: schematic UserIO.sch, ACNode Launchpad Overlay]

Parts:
J6: Conn_01x04_Female; PinHeader_1x04_P2.54mm_Vertical
SW1, SW2: SW_Push; SW_PUSH_6mm

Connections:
+5V: J6.1; also elsewhere on the board
BigButton: SW2.2; also elsewhere on the board
GND: J6.2, SW1.1, SW2.1; also elsewhere on the board
I2C_SCL: J6.3; also elsewhere on the board
I2C_SDA: J6.4; also elsewhere on the board
~Reset: SW1.2; also elsewhere on the board

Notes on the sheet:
Display
0.96" OLED I2C Display Displays system status, making maintainence and debugging easier
Buttons
Reset Button
The Button (Doorbell/Reader Button)

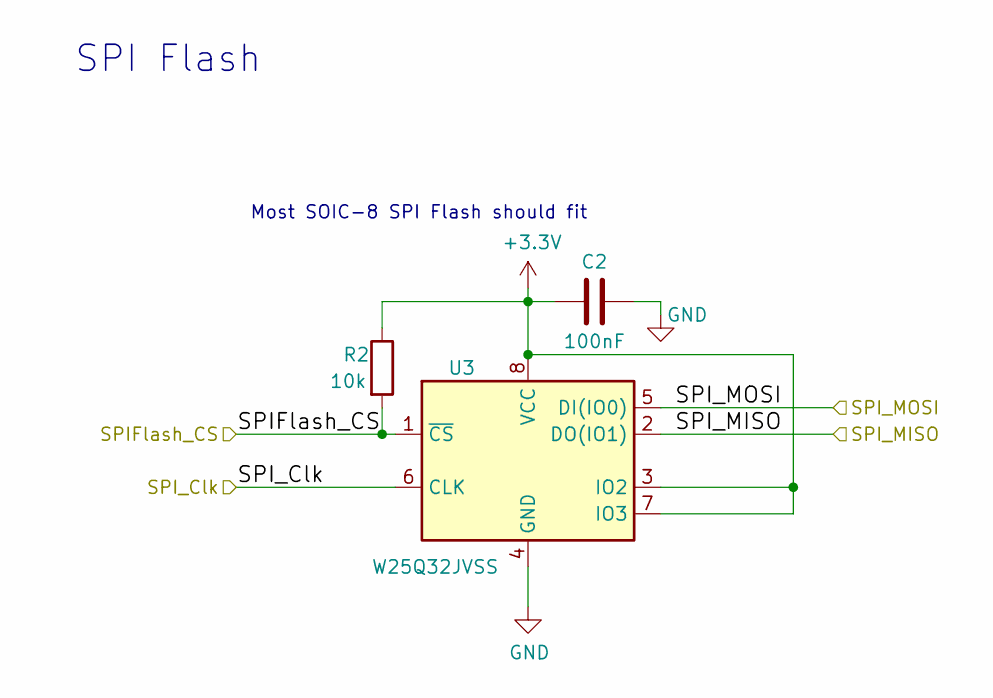
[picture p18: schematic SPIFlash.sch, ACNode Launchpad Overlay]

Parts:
C2: 100nF; C_0603_1608Metric
R2: 10k; R_0603_1608Metric
U3: W25Q32JVSS; SOIC-8_5.23x5.23mm_P1.27mm

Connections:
+3V3: C2.2, R2.1, U3.3 (IO2), U3.7 (IO3), U3.8 (VCC); also elsewhere on the board
/SPIFlash_CS: R2.2, U3.1 (~CS); also elsewhere on the board
/SPI_Clk: U3.6 (CLK); also elsewhere on the board
/SPI_MISO: U3.2 (DO(IO1)); also elsewhere on the board
/SPI_MOSI: U3.5 (DI(IO0)); also elsewhere on the board
GND: C2.1, U3.4 (GND); also elsewhere on the board

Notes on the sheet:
Most SOIC-8 SPI Flash should fit
SPI Flash

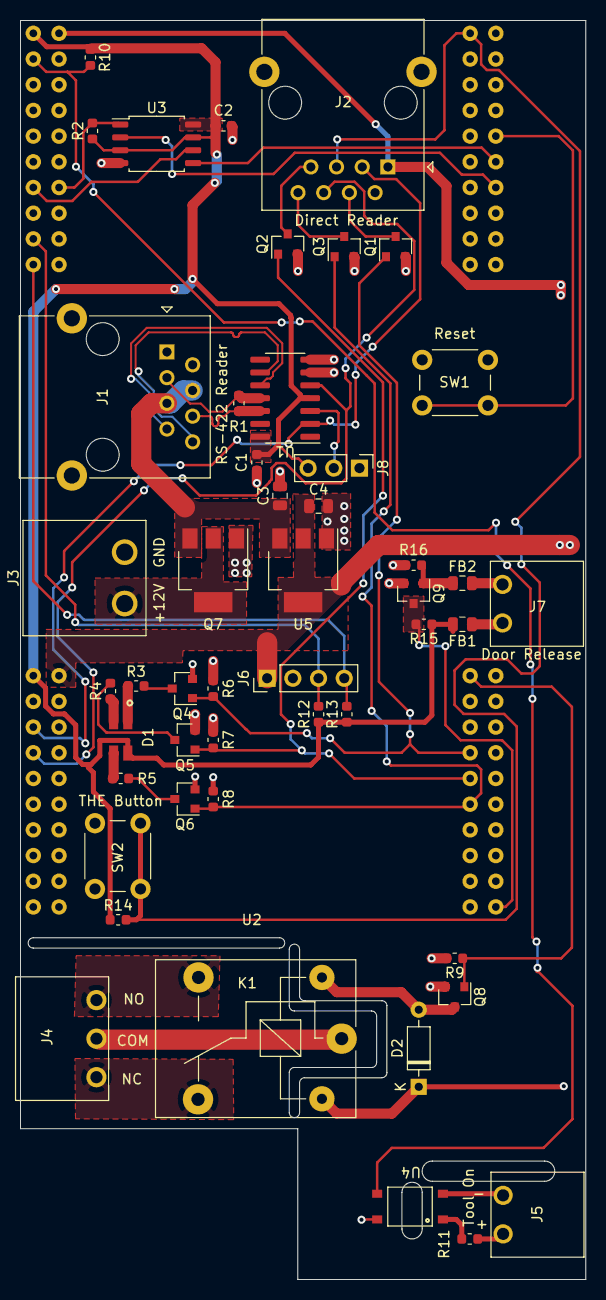
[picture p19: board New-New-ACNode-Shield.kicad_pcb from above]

Board: 2 copper layers, 55.9 x 124.5 mm, 49 parts (0 on the bottom side), 45 nets.

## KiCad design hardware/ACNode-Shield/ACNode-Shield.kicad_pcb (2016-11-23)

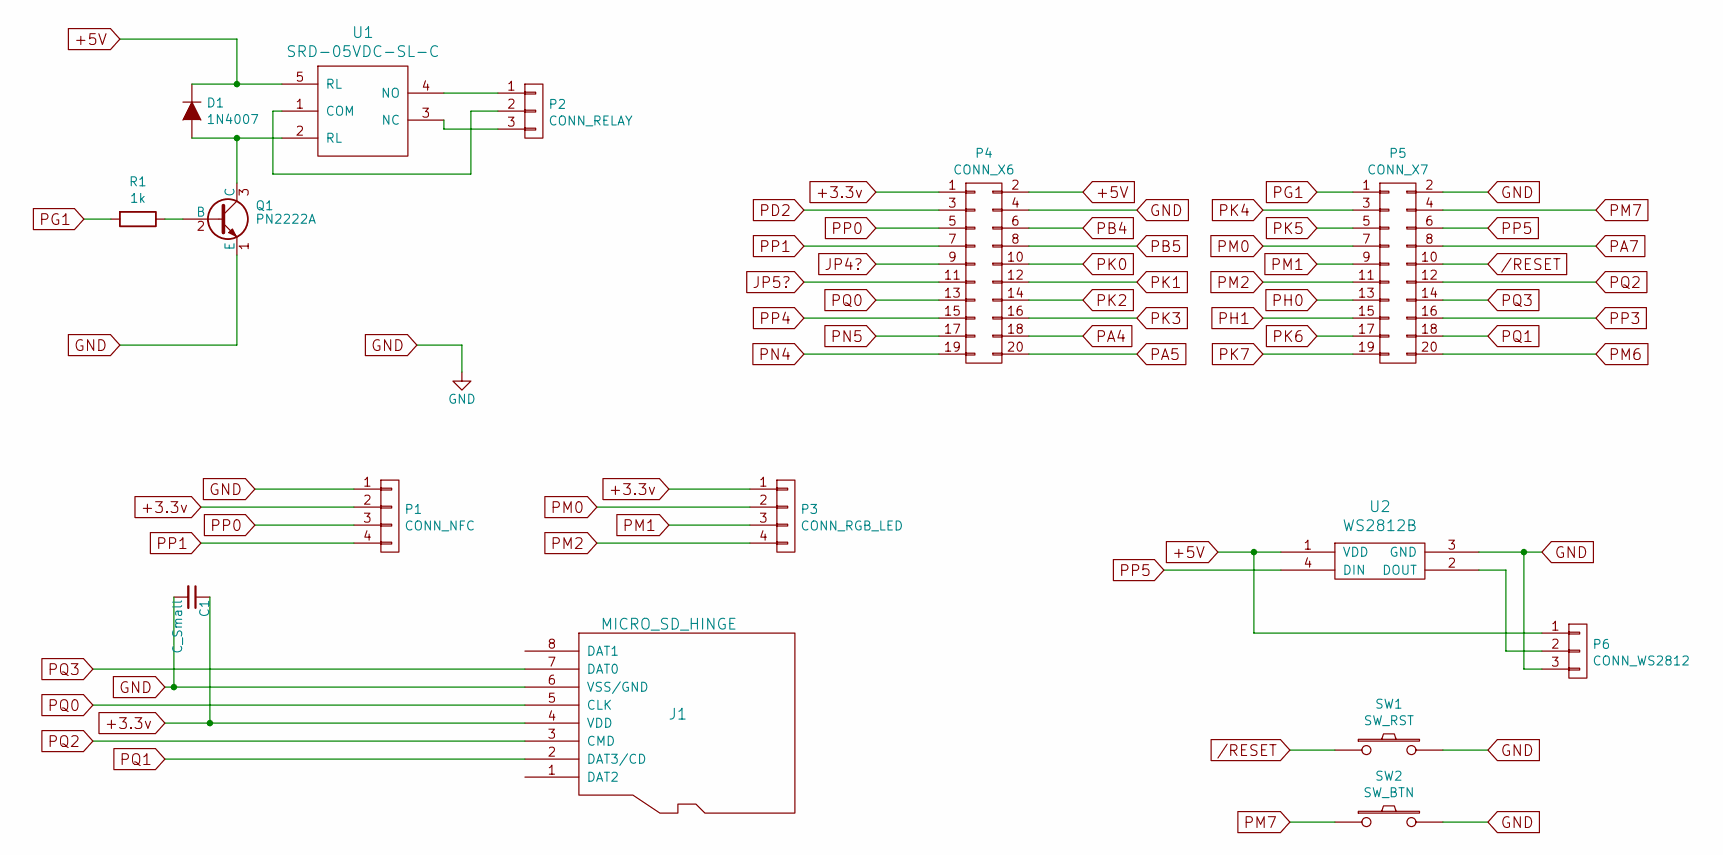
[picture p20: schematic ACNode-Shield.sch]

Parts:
C1: C_Small; C_1206
D1: 1N4007; Diode_DO-41_SOD81_Horizontal_RM10
J1: MICRO_SD_HINGE; MicroSD_Slot
P1: CONN_NFC; Pin_Header_Straight_1x04
P2: CONN_RELAY; TerminalBlock_Pheonix_MKDS1.5-3pol
P3: CONN_RGB_LED; Pin_Header_Straight_1x04
P4: CONN_X6; Socket_Strip_Straight_2x10
P5: CONN_X7; Socket_Strip_Straight_2x10
P6: CONN_WS2812; Pin_Header_Straight_1x03
Q1: PN2222A; TO-92_Inline_Wide
R1: 1k; Resistor_Horizontal_RM10mm
SW1: SW_RST; SW_PUSH_SMALL
SW2: SW_BTN; Socket_Strip_Straight_1x02
U1: SRD-05VDC-SL-C; Relay_SANYOU_SRD_Series_Form_C
U2: WS2812B; WS2812b

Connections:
+3.3v: C1.1, J1.4 (VDD), P1.2, P3.1, P4.1
+5V: D1.1 (K), P4.2, P6.1, U1.5 (RL), U2.1 (VDD)
/RESET: P5.10, SW1.1
GND: C1.2, J1.6 (VSS/GND), P1.1, P4.4, P5.2, P6.3, Q1.1 (E), SW1.2, SW2.2, U2.3 (GND)
JP4?: P4.9
JP5?: P4.11
unnamed: D1.2 (A), Q1.3 (C), U1.2 (RL)
unnamed: P2.1, U1.4 (NO)
unnamed: P2.2, U1.1 (COM)
unnamed: P2.3, U1.3 (NC)
unnamed: P6.2, U2.2 (DOUT)
unnamed: Q1.2 (B), R1.1
PA4: P4.18
PA5: P4.20
PA7: P5.8
PB4: P4.6
PB5: P4.8
PD2: P4.3
PG1: P5.1, R1.2
PH0: P5.13
PH1: P5.15
PK0: P4.10
PK1: P4.12
PK2: P4.14
PK3: P4.16
PK4: P5.3
PK5: P5.5
PK6: P5.17
PK7: P5.19
PM0: P3.2, P5.7
PM1: P3.3, P5.9
PM2: P3.4, P5.11
PM6: P5.20
PM7: P5.4, SW2.1
PN4: P4.19
PN5: P4.17
PP0: P1.3, P4.5
PP1: P1.4, P4.7
PP3: P5.16
PP4: P4.15
PP5: P5.6, U2.4 (DIN)
PQ0: J1.5 (CLK), P4.13
PQ1: J1.2 (DAT3/CD), P5.18
PQ2: J1.3 (CMD), P5.12
PQ3: J1.7 (DAT0), P5.14

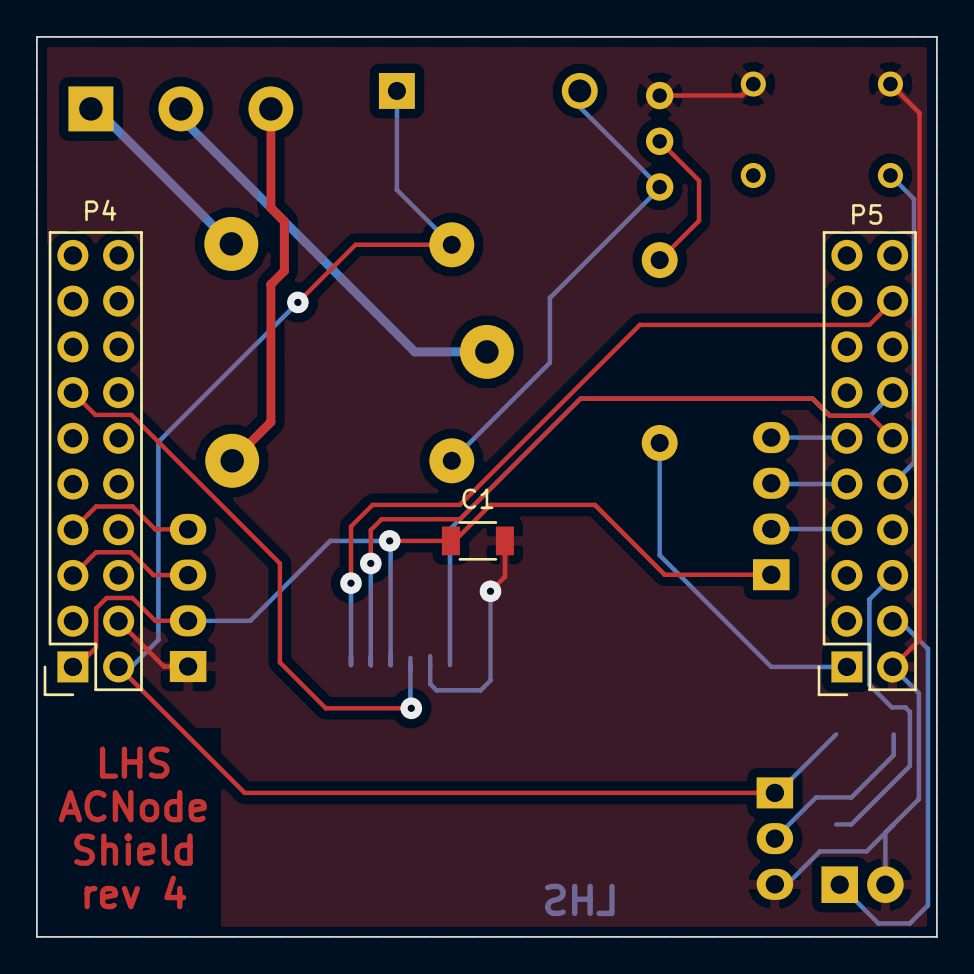
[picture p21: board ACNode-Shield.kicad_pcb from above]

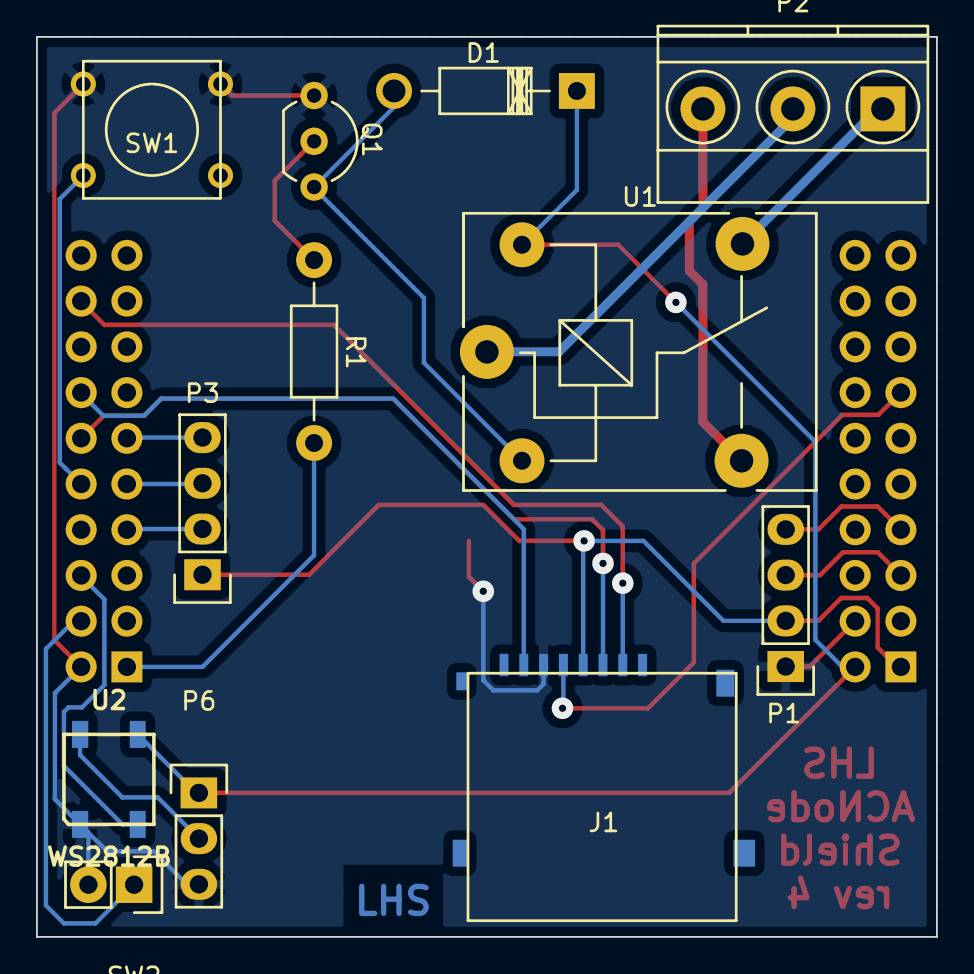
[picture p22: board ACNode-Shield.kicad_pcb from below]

Board: 2 copper layers, 50.0 x 50.0 mm, 15 parts (12 on the bottom side), 22 nets.

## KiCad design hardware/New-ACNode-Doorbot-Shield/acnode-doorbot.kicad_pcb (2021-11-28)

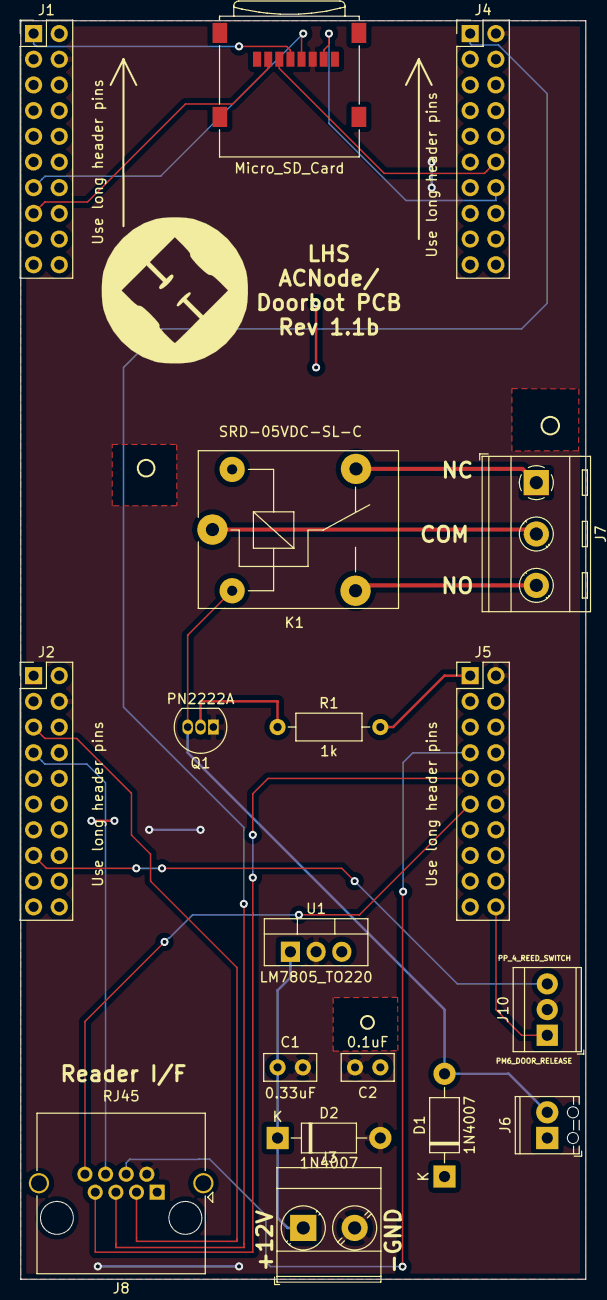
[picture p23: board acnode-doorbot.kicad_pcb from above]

Board: 2 copper layers, 55.9 x 124.5 mm, 18 parts (0 on the bottom side), 23 nets.

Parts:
C1: 0.33uF; C_Disc_D5.0mm_W2.5mm_P2.50mm
C2: 0.1uF; C_Disc_D5.0mm_W2.5mm_P2.50mm
D1, D2: 1N4007; D_DO-41_SOD81_P10.16mm_Horizontal
J1, J2, J4, J5: Conn_02x10_Odd_Even; PinHeader_2x10_P2.54mm_Vertical
J3: Screw_Terminal_01x02; TerminalBlock_Phoenix_MKDS-3-2-5.08_1x02_P5.08mm_Horizontal
J6: Screw_Terminal_01x02; TerminalBlock_Phoenix_MPT-0,5-2-2.54_1x02_P2.54mm_Horizontal
J7: Screw_Terminal_01x03; TerminalBlock_RND_205-00288_1x03_P5.08mm_Horizontal
J8: RJ45; RJ45_Amphenol_RJHSE5380
J9: Micro_SD_Card; microSD_HC_Wuerth_693072010801
J10: Screw_Terminal_01x03; TerminalBlock_TE_282834-3_1x03_P2.54mm_Horizontal
K1: SANYOU_SRD_Form_C; Relay_SPDT_SANYOU_SRD_Series_Form_C
Q1: PN2222A; TO-92_Inline
R1: 1k; R_Axial_DIN0207_L6.3mm_D2.5mm_P10.16mm_Horizontal
U1: LM7805_TO220; TO-220-3_Vertical

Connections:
3.3V: J1.1, J2.1, J9.4
5V: C2.1, D1.1, J1.2, J2.2, J6.1, J8.1, K1.5, U1.3
12V: C1.1, D2.1, J3.1, U1.1
GND: C1.2, C2.2, D2.2, J1.4, J2.4, J3.2, J4.2, J5.2, J8.2, J9.6, J10.2, Q1.1, U1.2
unnamed: D1.2, J6.2, K1.2, Q1.3
unnamed: J7.1, K1.4
unnamed: J7.2, K1.1
unnamed: J7.3, K1.3
unnamed: Q1.2, R1.1
PC_7: J1.15, J9.2
PD_0: J4.14, J9.7
PD_1: J4.12, J9.3
PD_3: J1.13, J9.5
PF_1: J4.1, J8.5
PG_1: J5.1, R1.2
PM_0: J5.7, J8.4
PM_1: J5.9, J8.7
PM_2: J5.11, J8.8
PM_6: J5.20, J10.1
PP_0: J2.5, J8.3
PP_1: J2.7, J8.6
PP_4: J2.15, J10.3
RST: J4.10, J5.10

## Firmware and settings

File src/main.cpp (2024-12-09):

#include <Arduino.h>
#include <Ethernet.h>

#include <PN532_debug.h>
#include <PN532_HSU.h>
#include <PN532.h>
#include <syslog.h>
#include <SPI.h>
#include <SD.h>
#include <OneMsTaskTimer.h>

#include "broadcastannouncer.h"
#include "mqttannouncer.h"
#include "settings.h"
#include "microrl.h"
#include "cli.h"
#include "cacheoverlay.h"
#include "card.h"
#include "utils.h"
#include "tool.h"
#include "network.h"
#include "acnode.h"
#include "rgb.h"
#include "colour.h"
#include "every.h"
#include "version.h"
#include "watchdog.h"
#include "cache.h"
#include "card.h"
#include "sdcache.h"
#include "eepromcache.h"
#include "ramcache.h"
#include "doorbot.h"
#include "doorbot_ac.h"
#include "maintainercachemaintainer.h"
#include "ACServer/RealACServer.h"

// create microrl object and pointer on it
microrl_t rl;
microrl_t * prl = &rl;

// PN532_HSU pnhsu(Serial6, PD_2);
PN532_HSU pnhsu(Serial6);
PN532 nfc(pnhsu);

EthernetClient client;
Syslog syslog;

boolean network = false;

// PG_1 to switch tool on, PE_4 is low when the tool is running
Tool tool(PG_1, PE_4);

RGB rgb(PM_0, PM_1, PM_2);

Watchdog wdog;

Cache *cache = NULL;
MaintainerCacheMaintainer* mcmaintainer = nullptr;
ACServer* acserver = nullptr;

Door *door = NULL;
Doorbot *doorbot = NULL;
ACNode *acnode = NULL;
int active_role;
Announcer* announcer = NULL;
int alive_check_count = 0;

Every am_i_alive(60000);

#define BUTTON_PIN PF_1
#define DOOR_RELEASE_PIN PM_6
#define SD_CS_PIN PC_7
#define ACNODE_DIR "ACNODE"

void serviceLed() { rgb.run(); };
OneMsTaskTimer_t ledBlinker = { 300, serviceLed, 0, 0 };

void setup() {
  Serial.begin(9600);
  Serial.println("");
  print_buildinfo();
  Serial.println("Starting up.");
  // lets use all the LED's
  pinMode(D1_LED, OUTPUT);
  pinMode(D2_LED, OUTPUT);

  digitalWrite(D1_LED, HIGH); // heartbeat
  digitalWrite(D2_LED, LOW);  // lit when we detect a card

  // used for ethernet link and activity
  pinMode(D3_LED, OUTPUT);
  pinMode(D4_LED, OUTPUT);

  // start the watchdog early in case of hangs
  wdog.begin();

  // need settings to configure the tool
  init_settings();

  acsettings = get_settings();
  dump_settings(acsettings);

  // start the tool early so it can be switched off(!?)
  tool.begin();

  // start the rgb early so we can get some feedback
  rgb.begin(acsettings.invert_colours == 1);

  // Workaround for a missing declaration in the library
  OneMsTaskTimer::add(&ledBlinker);
  rgb.rainbow();
  OneMsTaskTimer::start();

  wdog.feed();

  if (acsettings.sdcache) {
    if (SD.begin(SD_CS_PIN, SPI_HALF_SPEED, 2)) {
      Serial.println("SD card is accessible");
      SD.mkdir(ACNODE_DIR);
      cache = new SDCache("CACHE");
      Serial.println("Using the SD Card to cache cards");
    } else {
      Serial.println("SD card could not be accessed");
      Serial.println("Please fix the SD card and try again. Caching cards in RAM for now.");
      cache = new RAMCache();

      if(acsettings.maintainer_cache) {
        // insert overlay
        Cache* persistent = new EEPromCache();
        cache = new CacheOverlay(cache, persistent);
        acserver = new RealACServer(client, acsettings.servername, acsettings.port, acsettings.nodeid);
        mcmaintainer = new MaintainerCacheMaintainer(persistent, acserver);
      }
    }
  } else {
      Serial.println("Using the eeprom to cache cards");
      cache = new EEPromCache();
  }

  cache->begin();

  microrl_init (prl, mrlprint);
  // set callback for execute
  microrl_set_execute_callback (prl, mrlexecute);

  // set callback for completion
  microrl_set_complete_callback (prl, mrlcomplete);

  wdog.feed();

  // start the Ethernet connection. If the network is down this takes some time (60 secs?)
  // so disable the watchdog while it's happening
  wdog.disable();
  if (!Ethernet.begin(acsettings.mac)) {  
    Serial.println("Failed to configure Ethernet using DHCP");
  } else {
    network = true;
    Ethernet.enableLinkLed();
    Ethernet.enableActivityLed();
  }
  wdog.feed();
  wdog.enable();

  if (Ethernet.localIP() == INADDR_NONE) {
    Serial.println("Didn't get a valid ip");
    network = false;
  }

  if (network) {
    // print your local IP address:
    Serial.print("My IP address: ");
    for (byte thisByte = 0; thisByte < 4; thisByte++) {
      // print the value of each byte of the IP address:
      Serial.print(Ethernet.localIP()[thisByte], DEC);
      Serial.print(".");
    }
    Serial.println();
  }

  wdog.feed();

  if (!network) {
    syslog.offline();
  }

  syslog.begin(acsettings.syslogserver, acsettings.toolname, LOG_LOCAL0);
  char tmp[42];
  snprintf(tmp, 42, "Starting up, version %s", ACVERSION);
  syslog.syslog(LOG_NOTICE, tmp);

  if (wdog.was_reset()) {
    syslog.syslog(LOG_ALERT, "Alert! Was previously reset by the watchdog!");
  }
  wdog.feed();
  Serial.println("Determining announce_mode");
  switch(acsettings.announce_mode) {
    case 1:
      Serial.println("Broadcast announcer");
      if (network) {
        announcer = new BroadcastAnnouncer(acsettings.announce_port);
      } else {
        Serial.println("Would be Broadcast but no network");
        announcer = nullptr;
      }
      break;
    case 2:
      Serial.println("MQTT announcer");
      announcer = new MQTTAnnouncer(acsettings.mqtt_server, acsettings.mqtt_port, acsettings.mqtt_topic_base);
      break;
    default:
      Serial.println("No announcer");
      announcer = nullptr;
  }

  if(announcer) {
    Serial.println("Announcer starting");
    announcer->START();
  }

  door = new Door(PG_1, 0, acsettings.door_keep_open_ms);

  // The role may change when the user changes it via settings.
  active_role = acsettings.role;
  switch (active_role) {
    case 1:
      Serial.println("Starting regular Doorbot role");
      doorbot = new Doorbot(*door, wdog, nfc, rgb, BUTTON_PIN, DOOR_RELEASE_PIN);
      doorbot->enableAnnouncer(announcer);
      break;
    case 2:
      Serial.println("Starting restricted Doorbot role");
      doorbot = new DoorbotWithAccessControl(*door, wdog, nfc, rgb, BUTTON_PIN, DOOR_RELEASE_PIN);
      doorbot->enableAnnouncer(announcer);
      break;
    default:
      Serial.println("Starting acnode role");
      acnode = new ACNode(nfc, rgb, tool, BUTTON_PIN);
      acnode->enableAnnouncer(announcer);
      break;
  }

  wdog.feed();

  Serial.println("Initialising Card reader...");

  nfc.begin();

  uint32_t versiondata = nfc.getFirmwareVersion();

  if (! versiondata) {
    Serial.println("Didn't find PN53x board");
    syslog.syslog(LOG_EMERG, "Couldn't find PN532 board");
    while (1); // halt
  }

  // Got ok data, print it out!
  Serial.print("Found chip PN5"); Serial.print((versiondata>>24) & 0xFF, HEX);
  Serial.print(", Firmware ver. "); Serial.print((versiondata>>16) & 0xFF, DEC);
  Serial.print('.'); Serial.println((versiondata>>8) & 0xFF, DEC);

  // Set the max number of retry attempts to read from a card
  // This prevents us from waiting forever for a card, which is
  // the default behaviour of the PN532.
  //
  // with the powerdown thing we don't need a long timeout
  // so use 16...
  nfc.setPassiveActivationRetries(0x10);

  // configure board to read RFID tags
  nfc.SAMConfig();

  wdog.feed();

  if (network) {
    Serial.println("Checking tool status");
    int status = networking::networkCheckToolStatus();

    if (status < 0) {
      network = false;
      Serial.println("acserver error");
      char tmp[42];
      snprintf(tmp, 42, "unable to contact acserver");
      syslog.syslog(LOG_ALERT, tmp);
    }

    if (status == 1 || status == 0) {
      if (acsettings.status != status) {
        // update them if they have changed.
        acsettings.status = status;
        set_settings(acsettings);
      }
    }

    wdog.feed();

    char tmp[42];
    snprintf(tmp, 42, "tool status: %s", acsettings.status ? "in service" : "out of service");
    syslog.syslog(LOG_INFO, tmp);
    snprintf(tmp, 42, "total runtime: ");
    duration_str(tmp + strlen(tmp), acsettings.runtime);
    syslog.syslog(LOG_INFO, tmp);
    rgb.solid(BLUE);
  } else {
    rgb.solid(ORANGE);
  }

  wdog.feed();

  Serial.println("press enter for a prompt");
}

void loop() {
  // put received char from stdin to microrl lib
  if (Serial.available()) {
    char c;
    c = Serial.read();
    microrl_insert_char (prl, c);
  }
  switch (active_role) {
    case 1:
    case 2:
      doorbot->run();
      break;
    default:
      acnode->run();
  }
  
  if(announcer)
  {
    announcer->run();
  }

  if(mcmaintainer && network)
  {
    mcmaintainer->run();
  }

  if (am_i_alive.check()) {
    if(announcer) {
      uint32_t firmwarever = nfc.getFirmwareVersion();
      announcer->ALIVE(firmwarever != 0);
    }
    // Some of the cache methods don't store time-to-live, so we will want to verify all cached entries every 30 times we do the alive announcement, which works out about every half an hour
    // For those that do store time-to-live, this has the useful side-effect of refreshing the TTL, which means a bit more useful runtime if networking to the acserver is lost.
    if (networking::have_valid_ip()) {
      syslog.online();
      if (alive_check_count > 29) {
        alive_check_count = 0;
        wdog.feed();
        rgb.flashing(BLUE);
        Serial.println("Cache refreshing");
        cache->verify();
        rgb.solid(BLUE);
      }
      alive_check_count++;
      if ((door->isOpen()) || (tool.status())) {
        alive_check_count=0; // Because verifying all the users takes a while, we want to do it at quiet times
      }
    } else {
      syslog.offline();
    }
  }
}

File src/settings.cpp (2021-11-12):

#include <Energia.h>
#include "settings.h"
#include "acnode.h"
#include "utils.h"

settings acsettings;

void init_settings(void) {
  // must be a multiple of 4 cos our eeprom is
  // read and written in 32 bit chunks.
  if (sizeof(acsettings) % 4 != 0) {
    Serial.print("acsettings wrong size, needs to be a multiple of 4: ");
    Serial.println(sizeof(acsettings));
    while (true) {
      ;
    }
  }

  Serial.print("setting left: ");
  Serial.println(384 - sizeof(acsettings));

  if (sizeof(acsettings) > 384) {
    Serial.print("acsettings wrong size, must be smaller than 384: ");
    Serial.println(sizeof(acsettings));
    while (true) {
      ;
    }
  }

  uint32_t ret;

  ret = EEPROMInit();

  if (ret != EEPROM_INIT_OK) {
    Serial.print("EEprom init error: ");
    Serial.println(ret);
  }
}

void dump_settings(settings acsettings) {
  print_buildinfo();

  if (acsettings.valid) {
    Serial.println("Using settings from eeprom");
  } else {
    Serial.println("Using default settings, please change!");
  }

  int i;
  char tmp[10];

  Serial.print("Tool: ");
  Serial.println(acsettings.toolname);

  Serial.print("Mac address: ");

  for (i = 0; i < 6; i++) {
    sprintf(tmp, "%02X", acsettings.mac[i]);
    Serial.print(tmp);
    if (i < 5)
      Serial.print(":");
  }
  Serial.println("");

  Serial.print("Server hostname: ");
  if (isprint(acsettings.servername[0])) {
    Serial.println(acsettings.servername);
  } else {
     Serial.println("!Invalid!");
  }

  Serial.print("Server API key: ");
  if (isprint(acsettings.secret[0])) {
    Serial.println(acsettings.secret);
  } else {
     Serial.println("Not Set!");
  }

  Serial.print("Port: ");
  Serial.println(acsettings.port);

  Serial.print("nodeid: ");
  Serial.println(acsettings.nodeid);

  Serial.print("status: ");
  if (acsettings.status == 0) {
    Serial.println("out of service");
  } else if (acsettings.status == 1) {
    Serial.println("in service");
  } else {
    Serial.println("invalid status");
  }

  Serial.print("Syslog Server: ");
  if (isprint(acsettings.syslogserver[0])) {
    Serial.println(acsettings.syslogserver);
  } else {
     Serial.println("!Invalid!");
  }

  Serial.print("Total runtime: ");
  duration_str(tmp, acsettings.runtime);
  Serial.println(tmp);

  Serial.print("Minimum on time: ");
  Serial.println(acsettings.minontime);

  Serial.print("Using ");
  if (acsettings.sdcache) {
    Serial.print("a SD Card");
  } else {
    Serial.print("the internal eeprom");
  }
  Serial.println(" to cache cards.");

  if(acsettings.maintainer_cache) {
    Serial.println("Maintainer cache enabled.");
  } else {
    Serial.println("Maintainer cache disabled.");
  }

  if (acsettings.netverbose) {
    Serial.println("Verbose network messages.");
  } else {
    Serial.println("Being quiet about the network.");
  }

  Serial.print("The tool will be powered on by switching the toolonpin ");
  if (acsettings.toolonpin_activehigh) {
    Serial.println("HIGH.");
  } else {
    Serial.println("LOW.");
  }

  Serial.print("The acnode will detect that the tool is running when the toolrunpin is ");
  if (acsettings.toolrunpin_activehigh) {
    Serial.println("HIGH.");
  } else {
    Serial.println("LOW.");
  }

  Serial.print("This node behaves like a: ");
  switch(acsettings.role) {
    case 0:
      Serial.println("regular acnode");
      break;
    case 1:
      Serial.println("doorbot");
      break;
    case 2:
      Serial.println("doorbot with access control");
      break;
    case 3:
      Serial.println("auditing only");
  }

  if (acsettings.role > 0) {
    if(acsettings.announce_mode == 1) {
        Serial.print("Announcer port: ");
        Serial.println(acsettings.announce_port);
    }
    Serial.print("Door Keep Open Milliseconds: ");
    Serial.println(acsettings.door_keep_open_ms);
  }

  Serial.print("Announcer in ");
  switch(acsettings.announce_mode) {
      case 0:
        Serial.print("Disabled");
        break;
      case 1:
        Serial.print("Broadcast");
        break;
      case 2:
        Serial.print("MQTT");
  }
  Serial.println(" mode");

  if(acsettings.announce_mode == 2) {
    Serial.print("MQTT Server: ");
    if(isprint(acsettings.mqtt_server[0])) {
      Serial.println(acsettings.mqtt_server);
    } else {
      Serial.println("!Invalid!");
    }

    Serial.print("MQTT Port: ");
    Serial.println(acsettings.mqtt_port);

    Serial.print("MQTT Topic Base: ");
    if(isprint(acsettings.mqtt_topic_base[0])) {
      Serial.println(acsettings.mqtt_topic_base);
    } else {
      Serial.println("!Invalid!");
    }
  }

  Serial.print("Invert Colours: ");
  Serial.println((acsettings.invert_colours == 1) ? "on" : "off");

}

uint8_t get_settings_version(void) {
  uint32_t scratch;
  EEPROMRead((uint32_t *)&scratch, 0, sizeof(scratch));
  return scratch & 0xff;
}
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

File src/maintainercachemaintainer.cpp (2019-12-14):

#include "maintainercachemaintainer.h"
#include "card.h"
#include "cache.h"
#include "ACServer/DataRecords.h"
#include "ACServer/ACServer.h"
#include <Arduino.h>

// Arduino.h brings in stupid declarations that clash with <functional>
#undef min
#undef max

// ugly hack for callbacks
static MaintainerCacheMaintainer* currentCacheMaintainer = nullptr;

void MaintainerCacheMaintainer::onCardCallback(Card u)
{
    if(currentCacheMaintainer)
    {
        currentCacheMaintainer->onCard(u);
    }
}

MaintainerCacheMaintainer::MaintainerCacheMaintainer(Cache* maintainerCache, ACServer* acserver) :
    currentCacheCount(0),
    tempCache(nullptr),
    tempCacheCount(0),
    maintainerCache(maintainerCache),
    acserver(acserver),
    checkMaintainers(600000), // check every 10 minutes
    init(true)
{
    
}

MaintainerCacheMaintainer::~MaintainerCacheMaintainer()
{

}

void MaintainerCacheMaintainer::run()
{
    if(init)
    {
        init = false;
        checkMaintainers.begin();
        doCheck();
    }
    else if(checkMaintainers.check())
    {
        doCheck();
    }
}

void MaintainerCacheMaintainer::onCard(Card u)
{
    // ignore stale entries
    if(!u.is_valid())
    {
        return;
    }

    for(uint8_t i = 0; i < tempCacheCount; ++i)
    {
        if(u == tempCache[i])
        {
            // abuse the valid flag to indicate we have seen it
            tempCache[i].set_valid(false);
            return;
        }
    }

    // not in our list? nuke it!
    u.set_valid(false);
    maintainerCache->set(u);
}

static uint8_t hexDigit2Int(char d)
{
    if(d >= '0' && d <= '9')
    {
        return d-'0';
    }

    if(d >= 'A' && d <= 'F')
    {
        return d-'A'+10;
    }

    if(d >= 'a' && d <= 'f')
    {
        return d-'a'+10;
    }

    return 0;
}

static Card str2Card(const char* str)
{
    int bytes = strlen(str)/2;

    uint8_t uid[7] = { 0 };

    for(int i=0; i < bytes; ++i)
    {
        uid[i] = (hexDigit2Int(str[2*i]) << 4 ) + (hexDigit2Int(str[(2*i)+1]));
    }

    return Card(uid, bytes == 7, true, true);
}

void MaintainerCacheMaintainer::doCheck()
{
    Serial.println("Checking maintainer cache");
    MaintainerListRecord* mlr = acserver->getToolMaintainers();

    if(!mlr)
    {
        Serial.println("Error while retrieving maintainer list");
        return;
    }

    if(mlr->isSuccess())
    {
        currentCacheCount = 0;
        Serial.print("Got ");
        Serial.print(mlr->count);
        Serial.println(" maintainers");

        tempCache = new Card[mlr->count];
        tempCacheCount = mlr->count;

        // first convert to the usual format
        for(uint8_t i = 0; i < mlr->count; ++i)
        {
            tempCache[i] = str2Card(mlr->maintainers[i]);
        }

        /*
            Right... So... This isn't hugely efficient but will work.
            The Cache API is a bit of a turd for this actually. For each card
            in the cache, we check it against our list. If it is in our list, we
            abuse the "valid" flag to mark it as processed. If not, we mark it as invalid
            in the maintainer cache. Anything then "valid" in our list is a new entry.
        */
        currentCacheMaintainer = this;
        maintainerCache->each(onCardCallback);
        currentCacheMaintainer = nullptr;
        for(uint8_t i = 0; i < tempCacheCount; ++i)
        {
            if(tempCache[i].is_valid())
            {
                maintainerCache->set(tempCache[i]);
            }
        }

        delete[] tempCache;
        tempCacheCount = 0;
    }
    else
    {
        Serial.print("Error getting maintainer list: ");
        if(mlr->error)
        {
            Serial.println(mlr->error);
        }
        else
        {
            Serial.println("Unknown Error");
        }
    }

    delete mlr;
}

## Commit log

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2014-10-02 some user stuff, add support for rebooting
    [cli.cpp]
2014-10-02 Just use a single serNum global Attempt to work without network Keep track of the current card Let a card skip a few reads Add command for nukeing the user cache Also stupid = vs. == Cache users. Don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
    [cli.cpp, settings.cpp]
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2014-10-07 add syslog support, fix some warnings
    [cli.cpp, microrl.h, settings.cpp]
2014-10-07 get the mac address from the user registers, fixes #7, and fix a few more warnings
    [settings.cpp]
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2014-10-10 Record and report the total runtime, and c cli command to reset it.
    [cli.cpp, settings.cpp, tool.cpp]
2014-10-14 Check for button presses, and add cards if a maintainer has the button pressed. Support HTTP/1.0 (solveing the mystery of the missing headers)
    [network.cpp]
2014-11-18 Reduce the number of retries when looking for cards so we don't wait for ages. Add the new button class. (no menu yet). Remove redundant delays and check_ser's Invert state of tool pin activation (wi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
    **N.B this version of the code is in an intermediate state and may not be 100% working**
    [button.cpp, tool.cpp]
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2014-11-28 Use a short timeout and the new PN532 powerdown thing so we can poll things faster.
    Use Every to not print debug out everytime.
    Still a work in progress, N.B. new version of the PN532 code needed (just git pull it).
2014-11-28 Now that we have a short timeout we don't need to switch between interactive and non-interactive mode, which gives us one less layer of complexitey
    Also tidy some debug stuff.
    [button.cpp]
2014-12-01 Use an Every for the heartbeat LED - avoids a wierd inadvertant pwm thing.
    With the new powerdown/up code for the reader the temp card issue has
    gone, so remove the grace period stuff, making this all a little simpler :)
2014-12-01 move the code that we call when we have a valid card code to it's own function.
    tidy things up a bit
    timeout adding a new card rather than waiting for ever.
    handle led's a bit better.
2014-12-03 keep state of what colour we are to avoid more flickering
    [rgb.cpp]
2014-12-03 make the led's a bit nicer
    don't syslog if !network
    (you will need to update the syslog library with this version)
    fix user state logic stuff
    fix running with no network.
    Add a file listing the things we need to test (TESTING.txt)
2014-12-04 debounce a bit since we now sample the button much more often
2014-12-04 Add button menus for maintainers and users Users can now take a tool out of service Maintainers can take a tool out of service or put it in service Which together fixes #12
    Please read the readme for details on the menus
    We are (hopefully!) feature complete, make this a beta version, needs testing against the real acserver!
2014-12-14 switch the tool off when it is marked as out of service, bump to beta 2
2014-12-22 tidy a bit, mark the current card as invalid for the 1st run through the loop
2014-12-23 DXF for launchpad mounting holes
    [launchpad-footprint.dxf]
2014-12-23 don't invert the ssr pin
    [tool.cpp]
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2014-12-23 lasercut this to mount the launchpad, you want backing-frame.dxf
    [backing-frame.dxf, backing-v1.dxf]
2014-12-28 measure the tool run time, rather than switched on duration. Report total runtime properly
2015-01-06 toolid is 32 bit so can be 10 chars long, bump path length to avoid overflows
    [network.cpp]
2015-02-19 if the board does not have valid settings, save the default ones. For some reason this makes the card reader work :/ see issue #15
    [settings.cpp]
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2015-05-09 also check for errors properly when we are switching the tool on
    [network.cpp]
2015-05-09 When the tool is running don't check the tool status more than once every 2 secs.
    When initially checking on the tool status, if we get a network
    error, mark thge network as down.
    When we check the card status, if we get a reply from the
    network, mark the network as working.
    Only report toolusage if the network is running.
    N.B. compiled and tested with energia 15.
    [network.cpp, tool.cpp]
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2015-05-09 report errors corectly, set network to false if querycard fails
    [network.cpp]
2015-09-08 toolUse is not used so remove it, fixes issue #31
    [network.cpp]
2015-09-17 fill out class Card more little bit of tidying big struct user -> class Card changes fix a bug where there was a delay changing the colour of the button seems to work but needs testing more.
    [card.cpp, eepromcache.cpp, network.cpp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]
2015-09-23 Fix issue with all cards appearing to have a long uid
    [card.cpp, eepromcache.cpp]
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2015-09-26 Warn if the tool starts or stops running when it is switched off, fixes #37
    [tool.cpp]
2015-09-27 Fix some stuff in sdcache:
    * APPEND really only appends, so don't use it
    * in WRITE mode the file position starts at the end, so seek to the beginning
    * seek() takes a uint32_t, so trying to seek to a negative offset does not work
    * the first entry could be invalid
    * fix off by one in compare()
    [sdcache.cpp]
2015-09-28 Try to fix vairous network timeout and packet mangling issues.
    possibly more visible now with netverbose off, since the with it on the serial.print() things add serendepitious delays which hid the issues.
    The symptom was that POSTing to /tooluse/ would return -1 about one time in 20 or so, usually beacause only the "200 OK" part was read from the network and the rest discarded.
    [network.cpp]
2015-10-07 terminate the ret buffer to avoid printing junk when the network is down
    [network.cpp]
2015-10-11 fix eepromcache not caching things
    [eepromcache.cpp]
2015-10-17 add support for a secret key shared with the server, fixes #29
    [cli.cpp, network.cpp, settings.cpp]
2016-03-29 Migrated to PlatformIO.
    [backing-frame.dxf, backing-v1.dxf, launchpad-footprint.dxf]
2016-04-12 Copied SPI library from Energia @ e39045530703f982b41d7c11bba6adb5d9ba22fe (hardware/lm4f/libraries/).
    Seems like platformio has Energia at v15.
2016-04-12 Added a friendly notice to remind us to remove the packaged SPI library from Energia 17.
2016-04-12 Moved hardware directory to the root.
    [backing-frame.dxf, backing-v1.dxf, launchpad-footprint.dxf]
2016-04-13 PlatformIO now has the latest Energia, but it still doesn't solve our problem with the SPI library.
2016-04-13 No longer need to include SPI library.
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2016-05-07 Initial commit.
    [ACNode-Shield.kicad_pcb, ACNode-Shield.sch]
2016-05-07 PCB rev 1
    [ACNode-Shield-B.Mask.gbr, ACNode-Shield-B.SilkS.gbr, ACNode-Shield-Bottom.gbr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]
2016-05-09 Simplified PCB, changed Micro SD slot footprint.
    [ACNode-Shield.kicad_pcb]
2016-05-09 Added a 2x2 matrix of PCBs.
    [ACNode-Shield-2x2.kicad_pcb]
2016-05-12 Removed a resistor, fixed some tracks.
    [ACNode-Shield.kicad_pcb, ACNode-Shield.sch]
2016-05-14 Moved components around, changed MicroSD card receptacle footprint (was flipped (!)).
    [ACNode-Shield.kicad_pcb, ACNode-Shield.sch]
2016-05-14 Generated 2x2 board matrix.
    [ACNode-Shield-2x2.kicad_pcb]
2016-05-14 Removed old outputs.
    [ACNode-Shield-B.Mask.gbr, ACNode-Shield-B.SilkS.gbr, ACNode-Shield-Bottom.gbr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]
2016-05-14 2x2 matrix, updated options for printing transparencies.
    [ACNode-Shield-2x2.kicad_pcb]
2016-05-14 Generated PDFs suitable for photoresist hobby production.
    [ACNode-Shield-2x2.kicad_pcb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]
2016-05-15 Design was mirrored, need to redo this whole thing from scratch.
    [ACNode-Shield-2x2.kicad_pcb, ACNode-Shield.kicad_pcb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]
2016-06-11 Updated MicroSD Card socket footprint, repositioned elements. Everything is on the correct layer.
    [ACNode-Shield.kicad_pcb, _saved_ACNode-Shield.sch]
2016-06-11 Off to the fab.
    [ACNode-Shield.kicad_pcb, ACNode-Shield.sch, _saved_ACNode-Shield.sch]
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2016-07-10 Fixed references to namespaced functions.
    [doorbot.cpp, doorbot_ac.cpp]
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2016-07-10 Changes to fix an odd error.
    [microrl.h]
2016-09-29 Updated the MicroSD slot component, based on precise drawings.
    [ACNode-Shield.kicad_pcb, ACNode-Shield.sch]
2016-09-29 I've made the component pads thicker, for easier soldering.
    [ACNode-Shield.kicad_pcb]
2016-09-30 Rev 2 off to the fab
    [ACNode-Shield-B.Cu.gbr, ACNode-Shield-B.Mask.gbr, ACNode-Shield-B.SilkS.gbr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]
2016-10-03 Updated via outlines to be 1.2mm for easier manufacture.
    [ACNode-Shield-B.Cu.gbr, ACNode-Shield-B.Mask.gbr, ACNode-Shield-B.SilkS.gbr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]
2016-10-04 Added some text on copper layers.
    [ACNode-Shield-B.Cu.gbr, ACNode-Shield-B.Mask.gbr, ACNode-Shield-B.SilkS.gbr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]
2016-11-04 Removed a single trace that wasn't needed.
    [ACNode-Shield.kicad_pcb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]
2016-11-07 Refactored how the LED works, adjusted callers to reflect the new interface.
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2016-11-13 Changed button pin to PM_7 to be compatible with the rev 2 of the board. User/maintainer menu now mostly works.
2016-11-13 RGB class supports two-colour flashing. A maintainer can take a tool online and offline. When activated by a maintainer the LED turns yellow, when by a user - green.
2016-11-13 Correct colouring based on different user types.
    [acnode.cpp]
2016-11-13 Implemented a simple caching mechanism in RAM. Feed the watchdog so it doesn't die while iterating over cards.
2016-11-21 Removed large SD card connector - it doesn't fit.
    [ACNode-Shield-B.Cu.gbr, ACNode-Shield-B.Mask.gbr, ACNode-Shield-B.SilkS.gbr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]
2016-11-22 Copper fill. Regenerated gerbers.
    [ACNode-Shield-B.Cu.gbr, ACNode-Shield-B.Mask.gbr, ACNode-Shield-B.SilkS.gbr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]
2016-11-23 Reversed contacts on the SD card connector - it should work now.
    Bumped revision of the board to 4.
    [ACNode-Shield-B.Cu.gbr, ACNode-Shield-B.Mask.gbr, ACNode-Shield-B.SilkS.gbr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]
2017-05-10 Added a rainbow cycle during bootup as a quick check if the LED is working.
    This relies on working OneMsTaskTimer.cpp implementation for which there will be a PR for in Energia.
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2017-05-20 Fixed a bug where a maintainer card wouldn’t light up as yellow.
    [acnode.cpp]
2017-05-20 Check if tool is enabled, every 30 seconds - force-checking when disabled every 500ms doesn't make sense. The led lights up as red when it is out of order.
    [acnode.cpp]
2017-05-20 Fixed a bug where when the menu was active and a card was removed, the menu would remain active.
    [acnode.cpp]
2017-05-20 Fix failing build. Included a patch that enables OneMsTaskTimer, a timer-based ticker for automatically updating the LED.
2018-08-02 get doorbot to handle lack of networking as fail-secure previously, with no connectivity to a working acserver process, it would misinterpret network failures as a grant of access for any card, (and 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
    [doorbot.cpp]
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2018-08-07 Fix key length in settings.cpp
    [settings.cpp]
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2018-08-26 Fix MQTT topic buffer overflow fail
    Turns out /door/gf-front-external/annoucements is longer than 32 characters
    [mqttannouncer.cpp]
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2018-09-04 correct pin for DOOR_RELEASE_PIN
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2018-09-08 bug on the popular AC node rev 2.0 board means that button_pin is now PF_1 instead of PM_7
    [main.cpp]
2018-10-26 MQTTAnnouncer: Don't leak like a sieve
    It turns out aJson.print(object) calls malloc to create a scratch space to
    write to. MQTTAnnouncer uses this function but does not free the memory,
    resulting in a leak of 256 bytes every time we send a message.
    This commit adds a "free" call to plug the leak.
    [mqttannouncer.cpp]
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2018-11-16 honor the netverbose setting correct some typos in messages
    [acnode.cpp, cli.cpp, eepromcache.cpp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]
2018-11-24 Fix a couple of buffer overruns in the MQTT code
    One was the template class for the MQTT client was set to a maximum length of 50 bytes,
    which is shorter than most of our messages. The other was a more subtle one where the
    card buffer didn't have room for a null terminator.
    [doorbot.cpp]
2018-12-25 Added the new redesigned PCB
    [acnode-doorbot-B.Cu.gbr, acnode-doorbot-B.Mask.gbr, acnode-doorbot-B.Paste.gbr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]
2019-02-15 From Liam: The RFID card holders to be lasercut to hold the cards in the readers.
    [Card front middle.dxf, Card front.dxf]
2019-02-21 some silkscreen documentation goodness
    [acnode-doorbot.kicad_pcb]
2019-02-26 Noticed that some cache storage classes don't store a time-to-live per entry, as such, they weren't expiring. Even those that do ttl were doing it rather dumb (it shouldn't expire if we don't have wo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
    Implement an automatic cache re-validation if we're idle for a long time
    If this turns out to take too long, will work out how to verify a
    smaller portion of the cache, but do it more frequently.
    [main.cpp]
2019-03-01 Improve cacheing refresh, implement colour code MAUVE that means that the card has been read, and it's waiting on a network response. If this colour stays on, it means that there's a networking probl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
    [doorbot.cpp, doorbot_ac.cpp]
2019-03-10 Make more robust in cases of network link failure
    When the network link goes down, the doorbot tries
    to do stuff anyway, which results in a generally nasty situation
    where it will probably hit enough timeouts to trigger the watchdog.
    This is bad because hitting the watchdog timer clears the cache, meaning
    people who otherwise would have been permitted access now are not.
    This commit adds checking of link status to a few key places. It's only
    a start, but it should help in the short term while a more thorough examination
    is performed.
    [doorbot.cpp, mqttannouncer.cpp]
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2019-03-10 Fix formatting, add link check to restricted doorbot
    [doorbot.cpp, doorbot_ac.cpp]
2019-03-10 Fix build fail on doorbot_ac
    [doorbot_ac.cpp]
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2019-03-18 Add announcements to acnode role, because sometimes things other than acserver might need to know the current in-use status of tools in a real-time basis (woodshop fan, for instance), rather than pol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
    Also, fixed the maintainer / inductee timeout, which was zero, now it
    allows 10 seconds to do the inductee card switcheroo, rather than
    swapping them like a cheap magician party trick with a tablecloth.
    [acnode.cpp, main.cpp, mqttannouncer.cpp]
2019-04-04 use the -j switch on GNU Make to increase the number of parallel jobs, this decreases the build time on most multi-core systems. You can set this to the number of cores, so -j8 is 8 cores, otherwise 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
2019-07-09 Fixed null pointer dereference in doorbot.cpp
    The announcer may be null when the node does not get DHCP.
    This commit checks for that null.
    [doorbot.cpp]
2019-07-12 CMakeLists: Fix Git SHA
    Without the git find module being run, the GIT_EXECUTABLE variable is
    not set, and hence the build does not get the SHA. This commit fixes this
    by calling the appropriate find module.
    [network.cpp, settings.cpp]
2019-07-12 Add git SHA to startup MQTT message
    Currently, the message on startup shows node version, which doesn't
    change nearly as much as the git sha, so this commit adds support for
    logging git sha.
    [mqttannouncer.cpp]
2019-08-21 A little rework and more get endpoints
    [RealACServer.cpp, network.cpp]
2019-09-10 Stop the EEProm cache from "borrowing" storage from the config
    The eeprom cache iteration logic contained a while(1) and no regard for the end of the eeprom. This results
    in it wrapping around, and trying to use the config as a card record, which, with validation, ends up modifying the
    config to make it no longer config. This is most unhelpful.
    This commit adds actual bounds validation to the EEProm cache logic. Novel idea, I know.
    [eepromcache.cpp]
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2020-08-25 Update docs feed the watchdog if you're typing commands set tool run start time by default to tool enabled time, which might help to prevent excessive tool run time
    [cli.cpp, tool.cpp]
2021-02-23 Added a new, hopefully improved board.
    It needs quite a lot of work still (see Readme.md) but it shows promise.
    [LED_Switching.sch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]
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2021-07-24 Make ACnode mode spam card announcements less
    The ACNode role spams cards way too much. This fixes it.
    Fixes #72
    [acnode.cpp]
2021-07-25 Create MQTT handler even if network is not present
    This means if the network recovers, it will then eventually reconnect.
    I've also checked DHCP, and it seems it does actually continuously retry (though it eventually tries
    every 60 seconds so it might take a little while to come up)
    I'm sure there are still some problems, however in summary, it's a step in the right direction
    [main.cpp, mqttannouncer.cpp, network.cpp]
2021-07-25 Add option to invert colours
    Current hardware requires driving the LED lines low to turn them on. The
    code therefore specifies all colours inverted.
    This method of driving the active low pins makes little sense, and more
    to the point, is incompatible with the newer hardware design, which uses
    buffer transistors to allow an on-board LED to be driven in parallel
    without loading the external LED.
    This commit fixes this insanity by making the inversion configurable
    (default on for compatibility) and defining the colours normally.
    [cli.cpp, main.cpp, rgb.cpp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]
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2021-08-09 Slightly reworked New-New-ACNode-Shield
    The ethernet connector was fouling the PCB, so this
    is an attempt to create a suitable cutout. It involves moving the tool running detection.
    [New-New-ACNode-Shield.kicad_pcb, New-New-ACNode-Shield.sch]
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2021-11-12 1.1b of Dawid's design, some cosmetic changes only.
    [acnode-doorbot-B.Cu.gbr, acnode-doorbot-B.Mask.gbr, acnode-doorbot-B.Paste.gbr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]
2021-11-12 slight tweaks I forgot to commit
    [acnode-doorbot.kicad_pcb]
2021-11-15 rebuilt Gerbers
    [New-New-ACNode-Shield-B_Cu.gbl, New-New-ACNode-Shield-B_Mask.gbs, New-New-ACNode-Shield-B_Paste.gbp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]
2021-11-18 Add watchdog reset to verify loop
    [eepromcache.cpp]
2021-11-23 DIN Rail clip.stl, based on github.com:Laser4DIY/Laser4DIY_Enclosure via openscad
    [dinrail_clip.stl]
2021-11-28 Following feedback from Arthur, the rev 1.1a silkscreen was noted to be incorrect. Updating repo in case someone orders more boards.
    Note errata in README.md
    [acnode-doorbot-B_Cu.gbl, acnode-doorbot-B_Mask.gbs, acnode-doorbot-B_Paste.gbp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]
2021-12-01 slight tweak to give better clamping when printed with PLA. 0.5mm tighter.
    [dinrail_clip.stl]
2021-12-07 Fix Schrodinger's maintainer problem in announcements
    On tools, when the user is a maintainer, an announcement will be sent indicating access was not granted, then it will fall through to the user case, which then sends a notification that access was granted.
    This is... not only wrong, but outright confusing.
    [acnode.cpp]
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2022-04-06 add simple breakout board for PCB-mounted RJ45 and right-angled board connector on back for Elechouse PN532 boards
    [acnode-reader-direct.kicad_pcb, acnode-reader-direct.kicad_sch]
2022-04-08 update with optional +5V output for button
    [acnode-reader-direct.kicad_pcb, acnode-reader-direct.kicad_sch]
2022-04-18 Update readme.md
    Errata on silkscreen
2022-04-18 rev 1.1a, including build photo of rev 1.1
    [acnode-reader-direct-B_Cu.gbl, acnode-reader-direct-B_Mask.gbs, acnode-reader-direct-B_Paste.gbp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]
2024-12-09 Fixed typo of incorrect string quotes
    [doorbot.cpp, doorbot_ac.cpp]
2024-12-09 FIxed unhandled enumeration in switch warnings
2024-12-09 Removed unused variables and fixed initialization order warnings
    [acnode.cpp, main.cpp, mqttannouncer.cpp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]
2024-12-09 Fixed signed/unsigned comparison warnings and "next = ++next" ambiguity
    [cli.cpp]
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
